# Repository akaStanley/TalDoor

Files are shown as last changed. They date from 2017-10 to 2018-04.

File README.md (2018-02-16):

# TalDoor (GatekeeperV2)
Spencer Kulbacki ~ CSH 2017-18

TalDoor (or GatekeeperV2) is a small POE door lock system that runs off the PocketBeagle and uses PN532 NFC module to scan and authenticate user ID cards and open the door.

## Hardware:
- [PocketBeagle](https://github.com/beagleboard/pocketbeagle)
- Pn532 NFC Module
- Esimated 500mA consumption of entire device during idle operation. Peak of 800mA during read/write  door motor operations. EST less than 3 WATT max POE requirements.

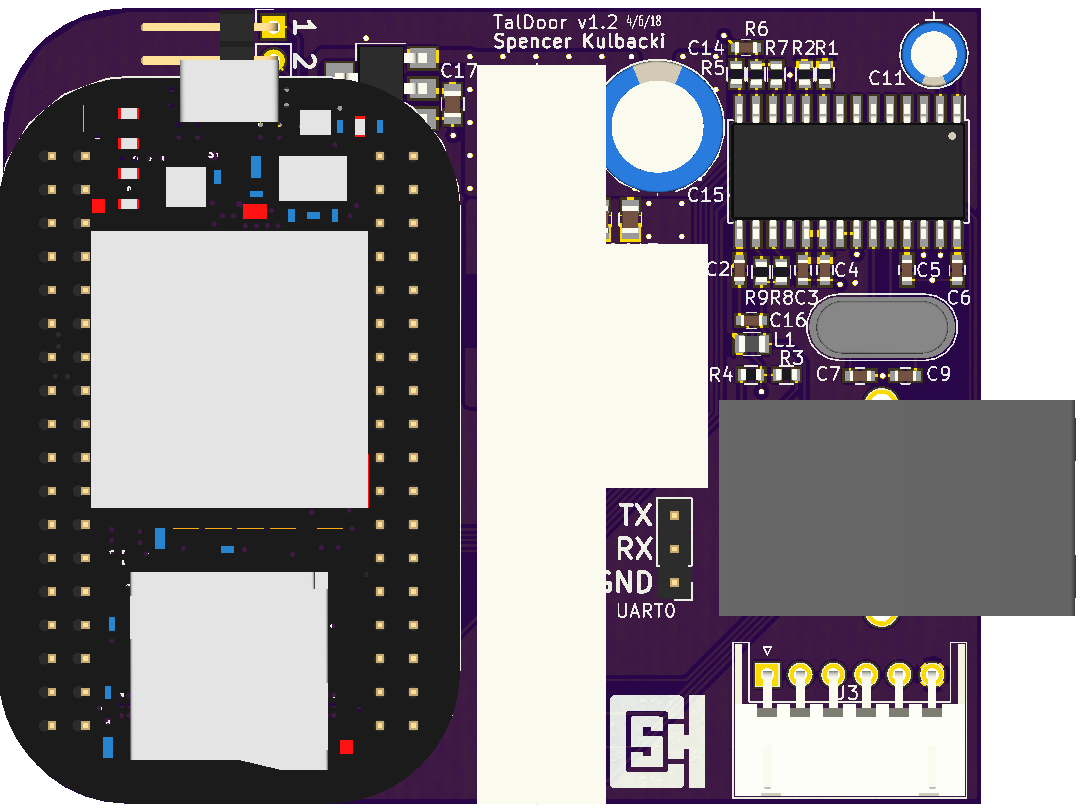
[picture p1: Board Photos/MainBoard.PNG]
Version 1.1 of the Main Board PCB.
  
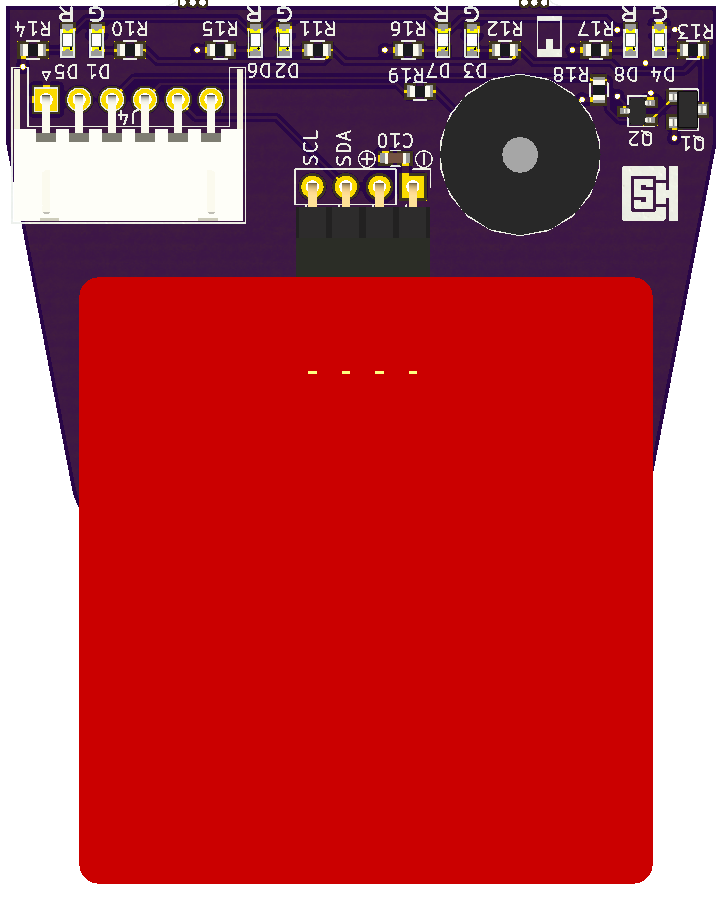
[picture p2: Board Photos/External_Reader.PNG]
Version 1.1 of the NFC Reader PCB.
  
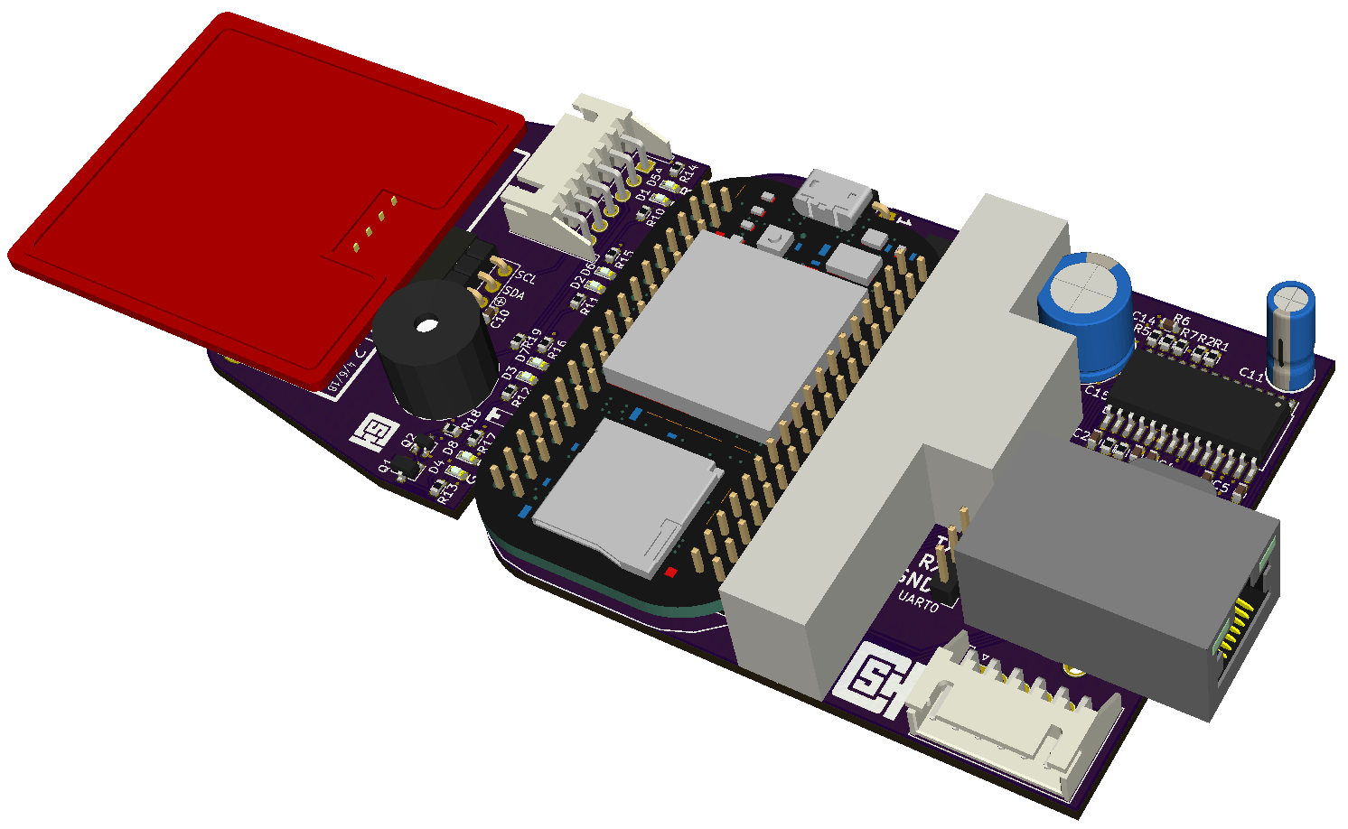
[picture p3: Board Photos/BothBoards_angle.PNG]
Version 1.1.
  

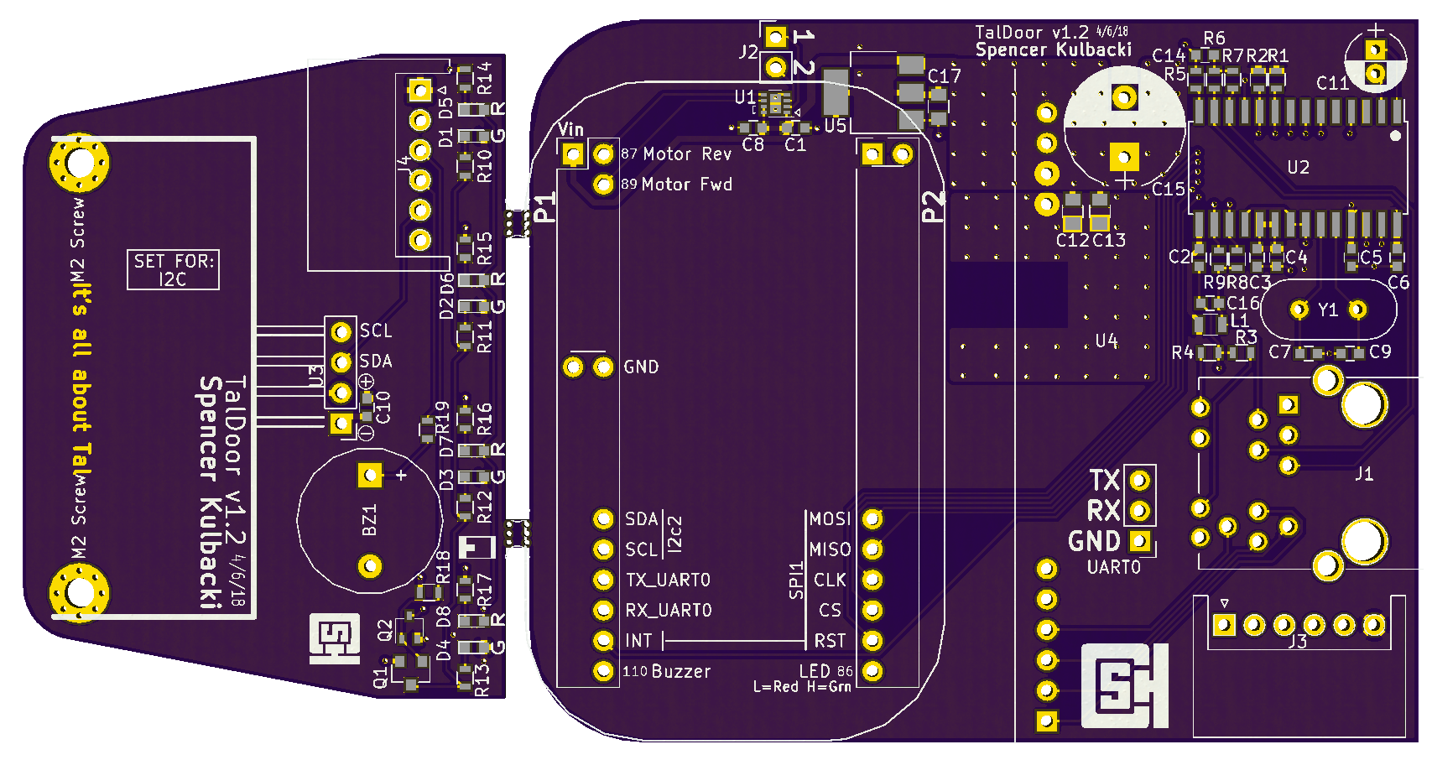
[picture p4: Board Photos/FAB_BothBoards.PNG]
Version 1.1 of the PCB.
  

### Internal Main Board contains:
- PocketBeagle
- POE module
- Ethernet to SPI module
- Door lock motor driver
- 3.3 to 5v step up for motor drive
	
### External Reader Board contains:
- PN532 NFC reader
- Red/Green LEDs & Beeper for notification

### Part List for the PCB
+/- some pin headers we already have
~30$ in components for one board (+PCB Cost)

~62 components specified in BOM (not counting extra male pin headers)

QTY|Value
----|------
1|Buzzer
9|0.1uF
2|18pF
3|10uF
1|10000pF
1|10uF
1|470uF
3|1uF
4|G_LED
4|R_LED
1|SI-52003-F_RJ45
1|Conn_01x02
2|Conn_01x06_Male
1|Ferrite_Bead
1|PocketBeagle
1|RK7002BM
1|BSS223PWH6327XTSA1
1|100kΩ
2|10kΩ
2|180Ω
1|2.2kΩ
4|49.9Ω
8|68Ω
1|150Ω
1|DRV8837
1|ENC28J60-I/SO
1|PN532
1|AG9703
1|NCP1117-3.3
1|25MHz

## Software:
- LibNFC 1.7.1

## Notes
- [Paul's Github notes](https://github.com/woo2/gatekeeper-v2/tree/master/notes)
- [BestCo door lock info,sorta](http://www.bestaccess.com/files/6014/6184/1926/WMseries_WEB.pdf)
- Setting up ethernet forwarding over USB for BeagleBone dev on a PC
	- Plugin the BeagleBone to a USB port on your computer
	- Install the drivers
	- In control panel -> Adapter settings, set the IP address of the USB adapter to 192.168.7.1
	- On the adapter that has the internet connection, enable connection sharing with the USB adapter connection
	- ssh into the BeagleBone (ssh 192.168.7.2)
	- Run command "route add default gw 192.168.7.1"
	- Edit /etc/resolv.conf and add the Google name server by adding the line "nameserver 8.8.8.8"
	
- Door locks are 5v motors that need ~70mA to turn a worm gear and "unlock" the turnkey.
- BeagleBoard uses 130mA nom (300mA peak)
- 4 Red 0603 LEDs use 80mA
- ENC28J60-I/SO uses 120mA nom (180mA peak)
- PN532 91mA nom (140mA peak)
- Esimated 500mA consumption of entire device during idle operation. Peak of 800mA during read/write  door motor operations. EST less than 3 WATT max POE requirements.

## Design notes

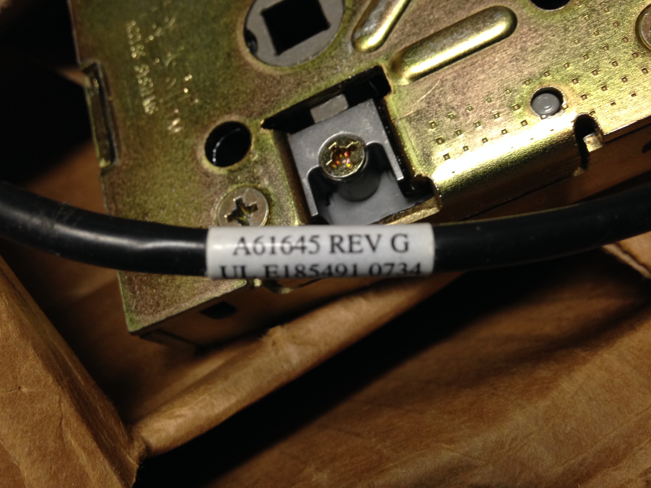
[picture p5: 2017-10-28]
Hardware/Reference/door_lock_motor_info (2).JPG

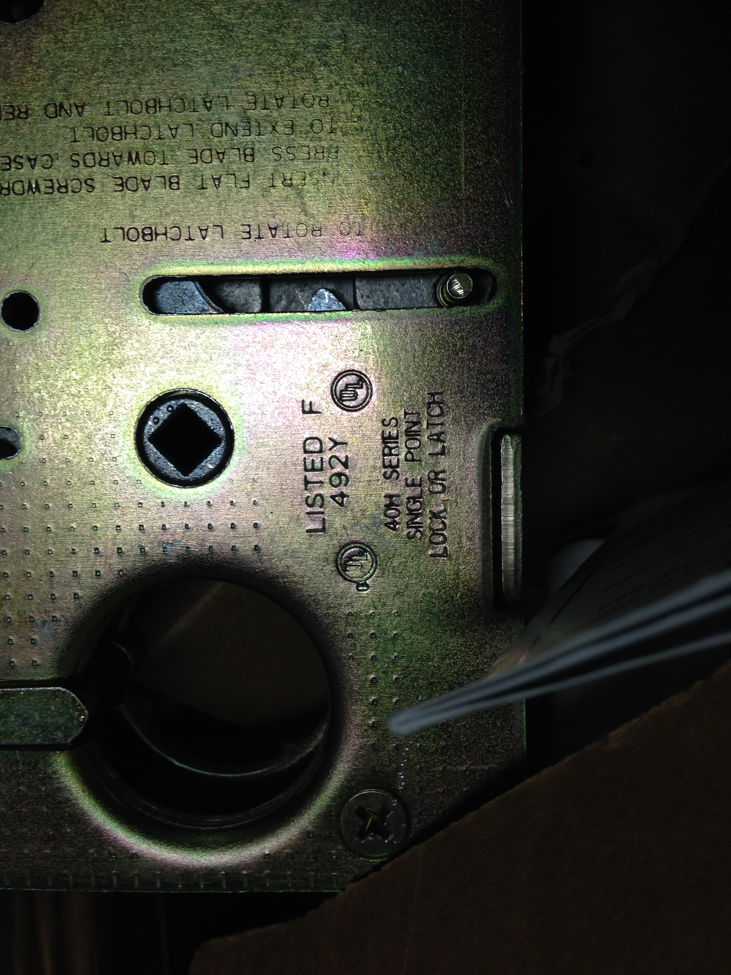
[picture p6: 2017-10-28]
Hardware/Reference/door_lock_motor_info (1).JPG

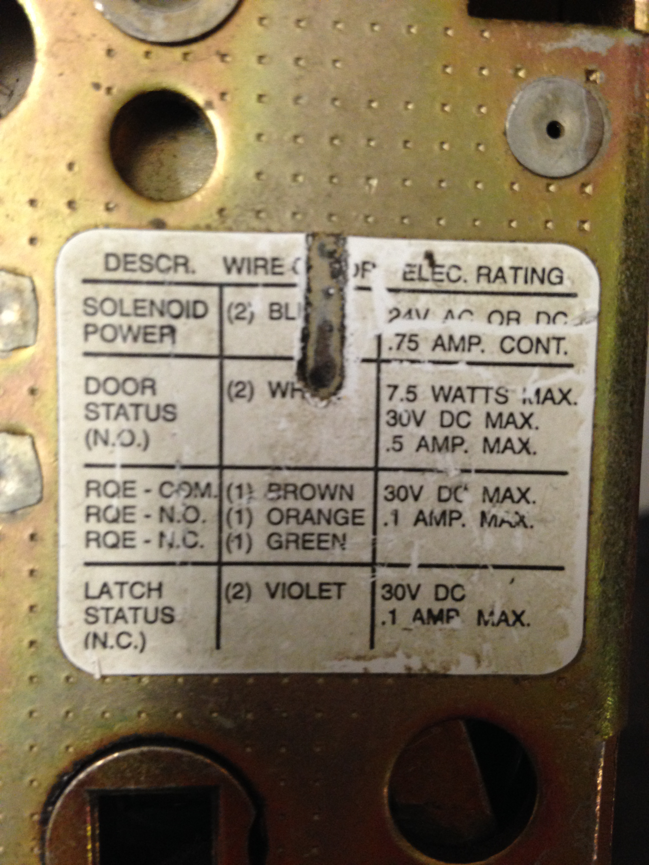
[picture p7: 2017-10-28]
Hardware/Reference/door_lock_motor_info.JPG

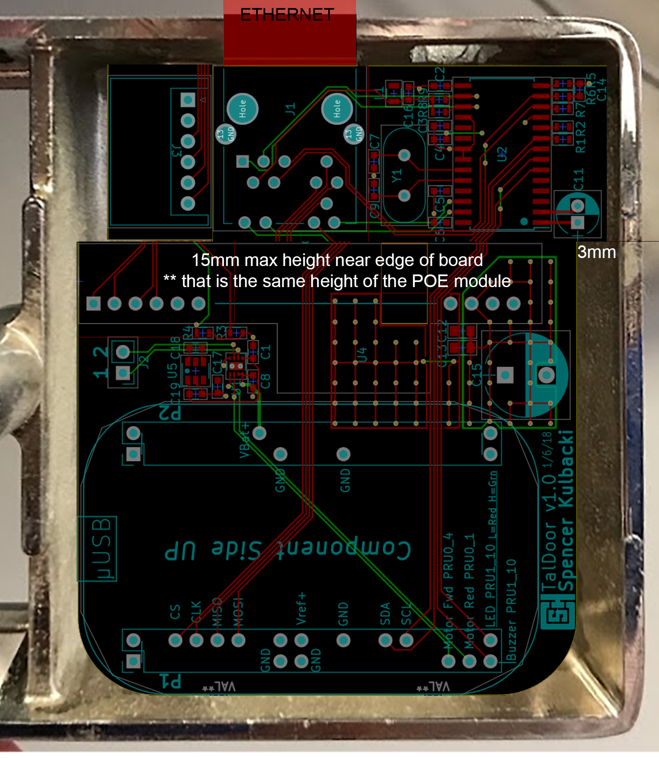
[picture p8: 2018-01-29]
Hardware/Reference/Taldoor_Layout.png

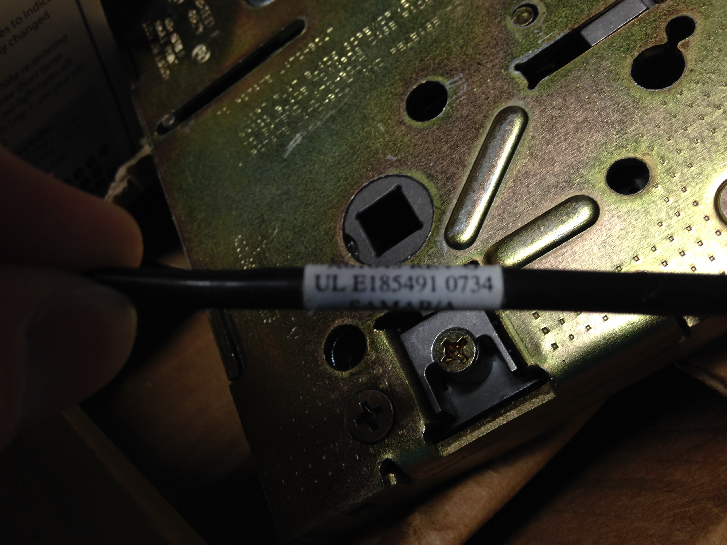
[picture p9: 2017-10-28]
Hardware/Reference/door_lock_motor_info (3).JPG

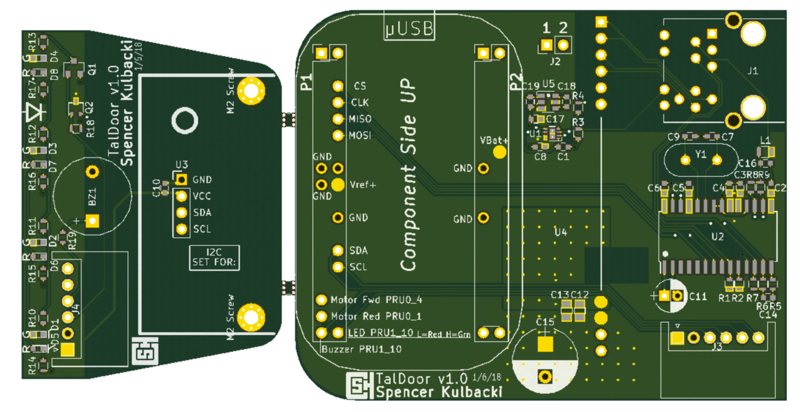
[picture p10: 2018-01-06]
Board Photos/FAB_BothBoards_v1.PNG

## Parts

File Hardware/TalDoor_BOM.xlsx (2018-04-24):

TalDoor PCB
Generated: 4/8/2018 11:51:53 AM | 59
Component Count: | 59
Ref | QTY | Value | Footprint | Description | Digikey Part # | Per Unit | Cost | Notes
BZ1, | 1 | Buzzer | Buzzers_Beepers:Buzzer_12x9.5RM7.6 | Buzzer, polar | 668-1456-ND | 1.375 | 1.3750
C2, C3, C4, C5, C6, C16, C1, C8, C10, | 9 | 0.1uF | Capacitors_SMD:C_0603 | Unpolarized capacitor | 478-10054-1-ND | 0.0106 | 0.0954
C7, C9, | 2 | 18pF | Capacitors_SMD:C_0603 | Unpolarized capacitor | 1276-1089-1-ND | 0.0119 | 0.0238
C12, C13, C17 | 3 | 10uF | Capacitors_SMD:C_0805 | Unpolarized capacitor | 1276-1096-1-ND | 0.094 | 0.2820
C14, | 1 | 10000pF | Capacitors_SMD:C_0603 | Unpolarized capacitor | 1276-1132-1-ND | 0.0075 | 0.0075
C11, | 1 | 10uF | Capacitors_THT:CP_Radial_D5.0mm_P2.00mm | Polarised capacitor | 399-6597-ND | 0.105 | 0.1050
C15, | 1 | 470uF | Capacitors_THT:CP_Radial_D10.0mm_P5.00mm | Polarised capacitor | 493-11709-1-ND | 0.311 | 0.3110 | OLD taller one: 493-5907-1-ND
D2, D1, D3, D4, | 4 | G_LED | LEDs:LED_0603 | Green LED | VLMG1300-GS08CT-ND | 0.337 | 1.3480
D5, D6, D7, D8, | 4 | R_LED | LEDs:LED_0603 | Super Red LED | VLMS1300-GS08CT-ND | 0.317 | 1.2680
J1, | 1 | SI-52003-F_RJ45 | TalDoor_Footprints:RJ45_POE | TH RJ45 with transformer + leds | 380-1119-ND | 5.11 | 5.1100 | No EMI Fingers, but different pinout: ARJ11D-MDSD-A-B-FLT2-ND
J2, | 1 | Conn_01x02 | Pin_Headers:Pin_Header_Straight_1x02_Pitch2.54mm | Generic connector, single row, 01x02 |  |  | 0.0000
J4, J3, | 2 | Conn_01x06_Male | Connectors_JST:JST_XH_S06B-XH-A_06x2.50mm_Angled | Generic connector, single row, 01x06 | 455-2236-ND | 0.368 | 0.7360 | Cables: https://www.amazon.com/uxcell-2-54mm-JST-XH-Adapter-Extension/dp/B014IZWGGI
L1, | 1 | Ferrite_Bead | Inductors_SMD:L_0805 | Ferrite bead | 490-7821-1-ND | 0.141 | 0.1410
P1 | 1 | PocketBeagle | TalDoor_Footprints:PocketBeagle_TalDoor | double row, odd1/even2 numbering |  |  | 0.0000 | Bespoke Female/Male Pin Headers (SIP sockets?)
Q1, | 1 | RK7002BM | TO_SOT_Packages_SMD:SOT-23 | Transistor N-MOSFET (general) | RK7002BMT116CT-ND | 0.16 | 0.1600 | Nmos
Q2, | 1 | BSS223PWH6327XTSA1 | TO_SOT_Packages_SMD:SOT-323_SC-70 | P-MOSFET with substrate diode BSS223PWH6327XTSA1 | BSS223PWH6327XTSA1CT-ND | 0.303 | 0.3030 | Pmos
R1, | 1 | 100kΩ | Resistors_SMD:R_0603 | Resistor | CR0603-JW-104ELFCT-ND | 0.008 | 0.0080
R2, R18, | 2 | 10kΩ | Resistors_SMD:R_0603 | Resistor | CR0603-JW-103ELFCT-ND | 0.016 | 0.0320
R3, R4, | 2 | 180Ω | Resistors_SMD:R_0603 | Resistor | RMCF0603JT180RCT-ND | 0.013 | 0.0260
R5, | 1 | 2.2kΩ | Resistors_SMD:R_0603 | Resistor | CR0603-JW-222ELFCT-ND | 0.016 | 0.0160
R9, R8, R7, R6, | 4 | 49.9Ω | Resistors_SMD:R_0603 | Resistor | CR0603-FX-49R9ELFCT-ND | 0.0099 | 0.0396
R14, R10, R11, R12, R15, R16, R13, R17, | 8 | 68Ω | Resistors_SMD:R_0603 | Resistor | CR0603-JW-680ELFCT-ND | 0.016 | 0.1280
R19, | 1 | 120Ω | Resistors_SMD:R_0603 | Resistor | CR0603-JW-121ELFCT-ND | 0.016 | 0.0160
U1, | 1 | DRV8837 | Housings_SON:WSON-8_1EP_2x2mm_Pitch0.5mm_ThermalVias | IC MOTOR DRIVER, 2 Half bridges | 296-34806-1-ND | 1.231 | 1.2310
U2, | 1 | ENC28J60-I/SO | Housings_SOIC:SOIC-28W_7.5x17.9mm_Pitch1.27mm | ENC28J60 Single Chip Ethernet Interface, SOIC-28 | ENC28J60-I/SO-ND | 2.756 | 2.7560
U3, | 1 | PN532 | Pin_Headers:Pin_Header_Straight_1x04_Pitch2.54mm | Pn532 NFC reader over I2C |  | 6.63 | 6.6300 | PN532
U4, | 1 | AG9705 | TalDoor_Footprints:Ag9700_FP | 48v POE stepdown transformer and voltage supply |  | 7.29 | 7.2900 | Ag9705-2BR
U5, | 1 | NCP1117-3.3_SOT223 | TO_SOT_Packages_SMD:SOT-223-3_TabPin2 | 1A Low Dropout regulator, positive, 1.5V fixed output, SOT-223 | 497-1228-1-ND | 0.603 | 0.6030
Y1, | 1 | 25MHz | Crystals:Crystal_HC49-4H_Vertical | Two pin crystal | 631-1112-ND | 0.32 | 0.3200
 |  |  |  |  |  | 30.3613

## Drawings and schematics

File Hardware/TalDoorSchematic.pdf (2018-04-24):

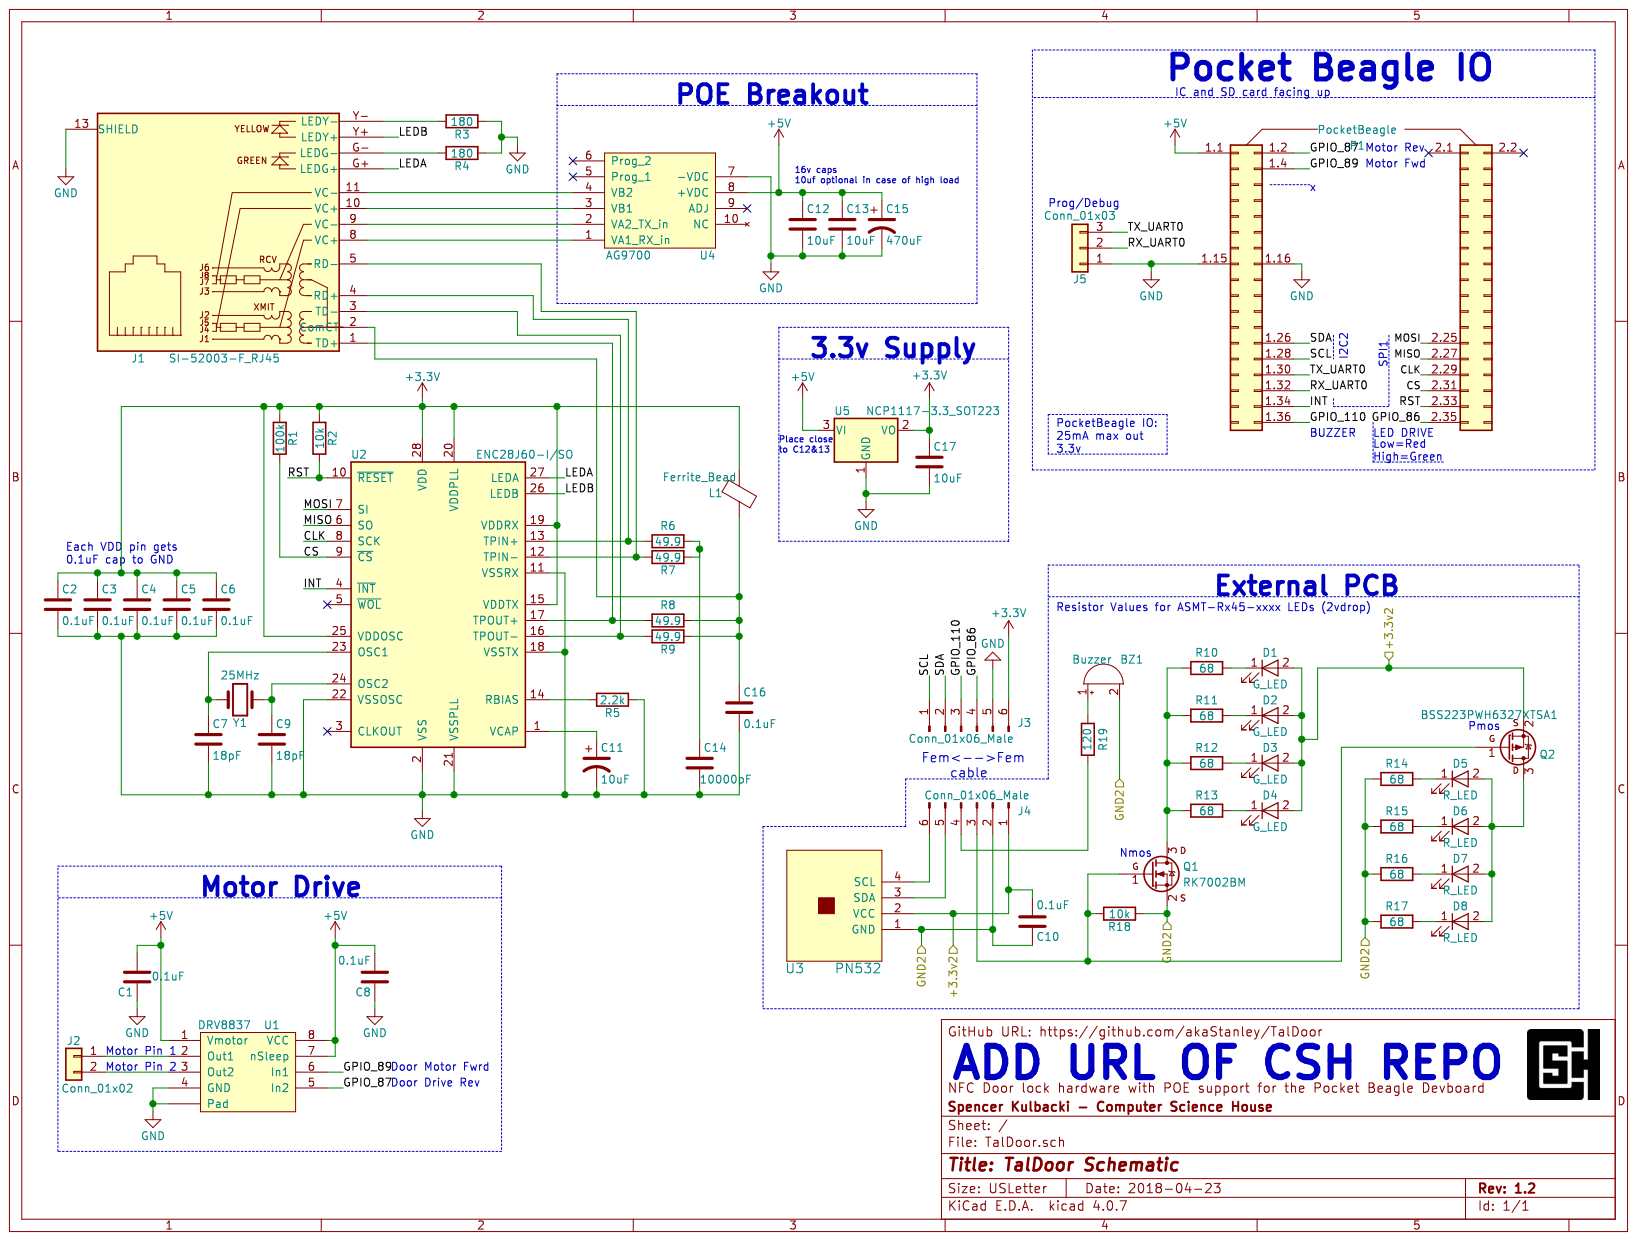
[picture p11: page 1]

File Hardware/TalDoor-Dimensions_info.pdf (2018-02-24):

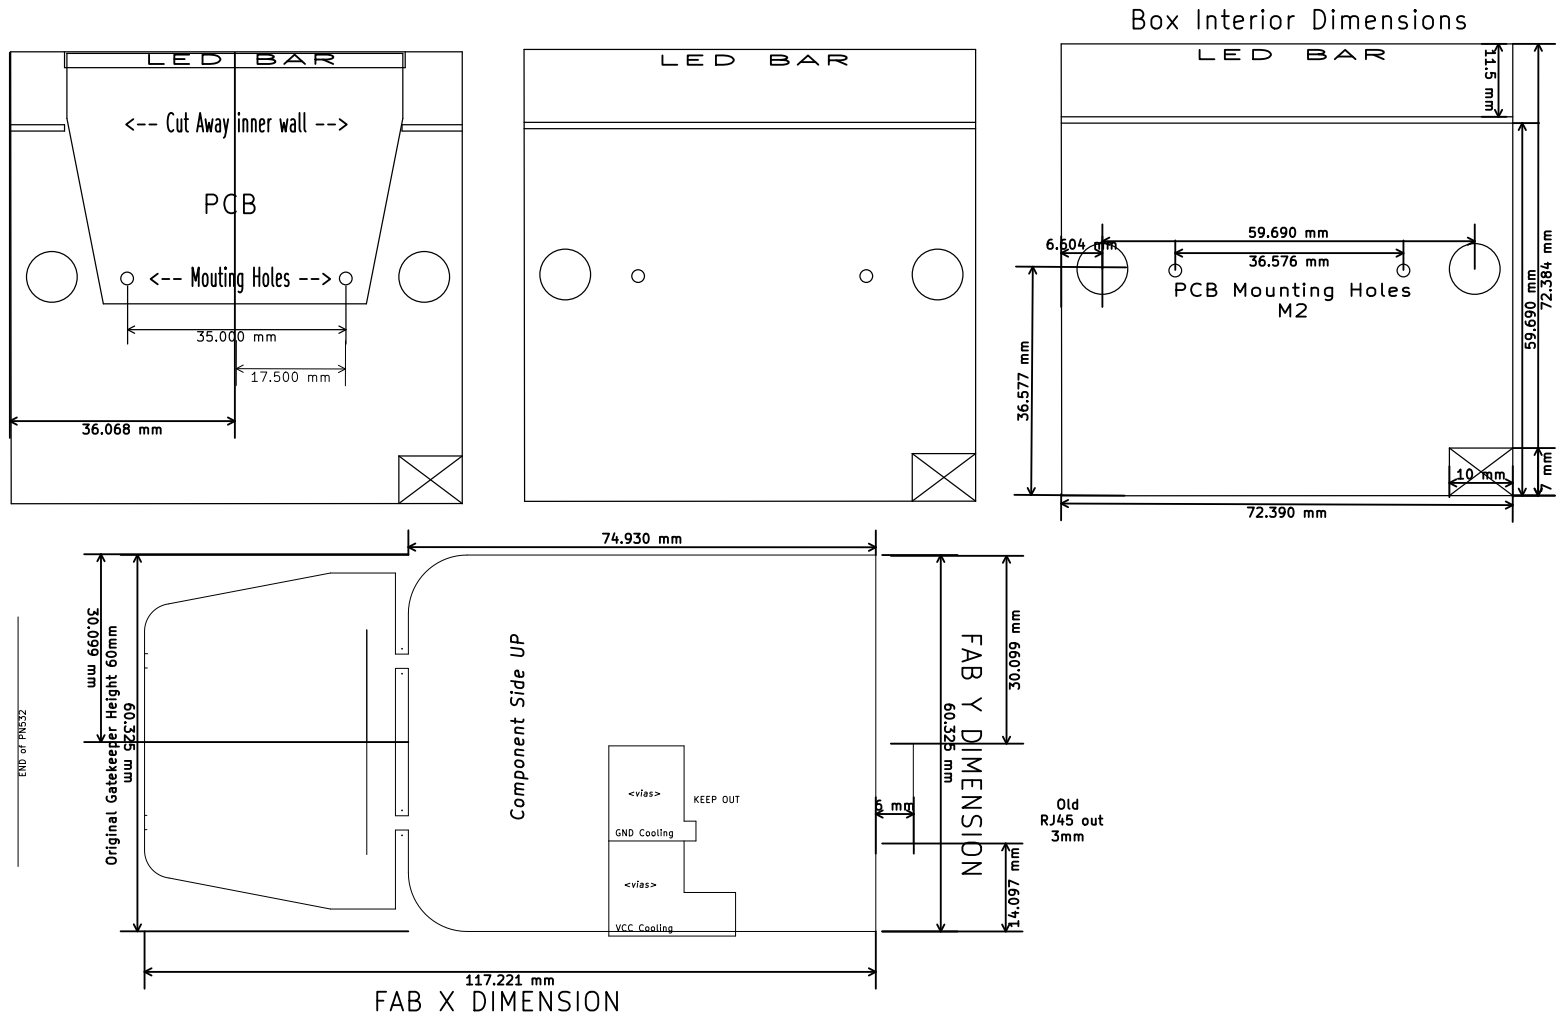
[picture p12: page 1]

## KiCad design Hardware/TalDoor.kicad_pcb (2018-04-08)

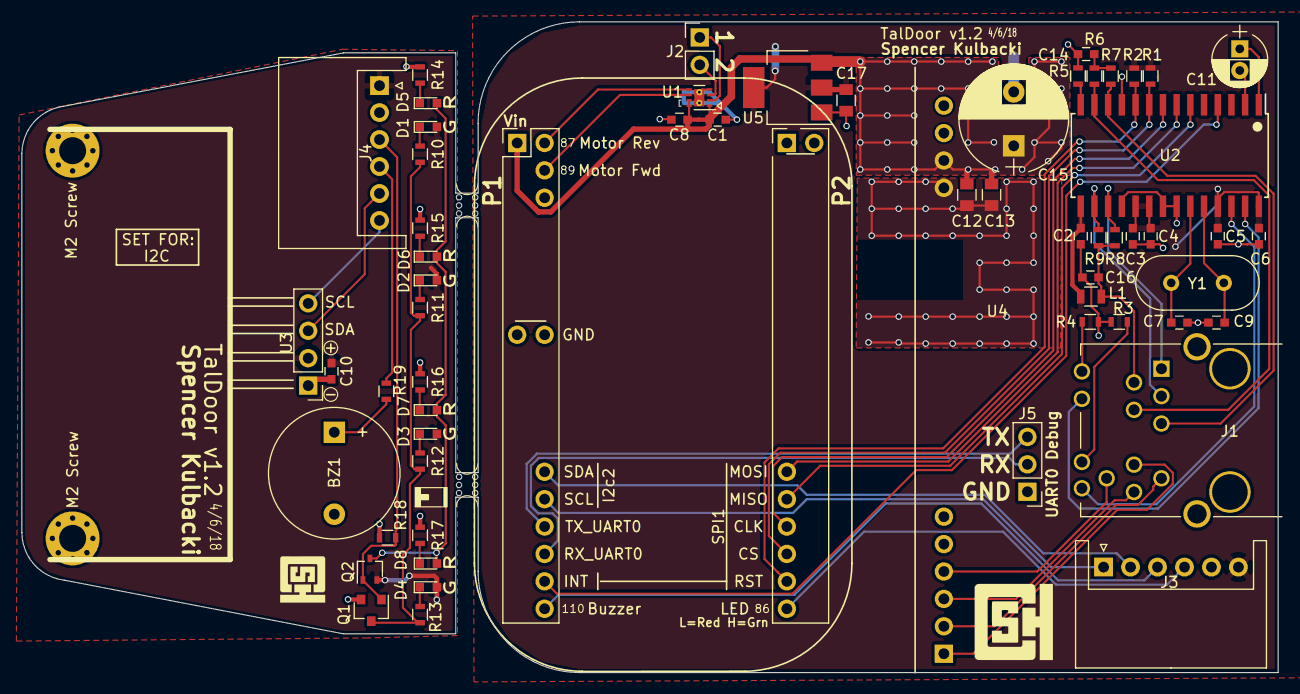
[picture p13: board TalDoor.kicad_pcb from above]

Board: 2 copper layers, 116.5 x 60.3 mm, 64 parts (0 on the bottom side), 54 nets.

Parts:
BZ1: Buzzer; Buzzer_12x9.5RM7.6
C1, C2, C3, C4, C5, C6, C8, C10, C16: 0.1uF; C_0603
C7, C9: 18pF; C_0603
C11: 10uF; CP_Radial_D5.0mm_P2.00mm
C12, C13, C17: 10uF; C_0805
C14: 10000pF; C_0603
C15: 470uF; CP_Radial_D10.0mm_P5.00mm
D1, D2, D3, D4: G_LED; LED_0603
D5, D6, D7, D8: R_LED; LED_0603
J1: SI-52003-F_RJ45; RJ45_POE
J2: Conn_01x02; Pin_Header_Straight_1x02_Pitch2.54mm
J3, J4: Conn_01x06_Male; JST_XH_S06B-XH-A_06x2.50mm_Angled
J5: Conn_01x03; Pin_Header_Straight_1x03_Pitch2.54mm
L1: Ferrite_Bead; L_0805
M2 Screw, M2 Screw#2: MountingHole_2.2mm_M2_Pad_Via; MountingHole_2.5mm_Pad_Via
P1: PocketBeagle; PocketBeagle_TalDoor
Q1: RK7002BM; SOT-23
Q2: BSS223PWH6327XTSA1; SOT-323_SC-70
R1: 100k; R_0603
R2, R18: 10k; R_0603
R3, R4: 180; R_0603
R5: 2.2k; R_0603
R6, R7, R8, R9: 49.9; R_0603
R10, R11, R12, R13, R14, R15, R16, R17: 68; R_0603
R19: 120; R_0603
U1: DRV8837; WSON-8_1EP_2x2mm_Pitch0.5mm_ThermalVias
U2: ENC28J60-I/SO; SOIC-28W_7.5x17.9mm_Pitch1.27mm
U3: PN532
U4: AG9700; Ag9700_FP
U5: NCP1117-3.3_SOT223; SOT-223-3_TabPin2
Y1: 25MHz; Crystal_HC49-4H_Vertical
mouse-bite-2mm-slot, mouse-bite-2mm-slot#2: VAL**; mouse-bite-2mm-slot

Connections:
+3V3: C2.1, C3.1, C4.1, C5.1, C6.1, C17.1, J3.6, L1.2, R1.1, R2.1, U2.15, U2.19, U2.20, U2.25, U2.28, U5.2
+5V: C1.2, C8.2, C12.1, C13.1, C15.1, P1.1.1, U1.1, U1.7, U1.8, U4.8, U5.3
/+3.3v2: C10.2, D1.2, D2.2, D3.2, D4.2, J4.1, Q2.2, U3.2
/CLK: P1.2.29, U2.8
/CS: P1.2.31, R1.2, U2.9
/GND2: BZ1.2, C10.1, J4.2, Q1.2, R14.2, R15.2, R16.2, R17.2, R18.1, U3.1
/GPIO_86: J3.4, P1.2.35
/GPIO_87: P1.1.2, U1.5
/GPIO_89: P1.1.4, U1.6
/GPIO_110: J3.3, P1.1.36
/INT: P1.1.34, U2.4
/LEDA: J1.G+, U2.27
/LEDB: J1.Y+, U2.26
/MISO: P1.2.27, U2.6
/MOSI: P1.2.25, U2.7
/RST: P1.2.33, R2.2, U2.10
/RX_UART0: J5.2, P1.1.32
/SCL: J3.1, P1.1.28
/SDA: J3.2, P1.1.26
/TX_UART0: J5.3, P1.1.30
GND: C1.1, C2.2, C3.2, C4.2, C5.2, C6.2, C7.2, C8.1, C9.2, C11.2, C12.2, C13.2, C14.2, C15.2, C16.2, C17.2, J1.13, J3.5, J5.1, P1.1.15, P1.1.16, R3.1, R4.1, R5.1, U1.4, U2.2, U2.11, U2.18, U2.21, U2.22, U4.7, U5.1
unnamed: BZ1.1, R19.2
unnamed: C7.1, U2.23, Y1.2
unnamed: C9.1, U2.24, Y1.1
unnamed: C11.1, U2.1
unnamed: C14.1, R6.1, R7.1
unnamed: C16.1, J1.2, L1.1, R8.1, R9.1
unnamed: D1.1, R10.1
unnamed: D2.1, R11.1
unnamed: D3.1, R12.1
unnamed: D4.1, R13.1
unnamed: D5.1, R14.1
unnamed: D5.2, D6.2, D7.2, D8.2, Q2.3
unnamed: D6.1, R15.1
unnamed: D7.1, R16.1
unnamed: D8.1, R17.1
unnamed: J1.1, R8.2, U2.17
unnamed: J1.3, R9.2, U2.16
unnamed: J1.4, R6.2, U2.13
unnamed: J1.5, R7.2, U2.12
unnamed: J1.8, U4.1
unnamed: J1.9, U4.2
unnamed: J1.10, U4.3
unnamed: J1.11, U4.4
unnamed: J1.G-, R4.2
unnamed: J1.Y-, R3.2
unnamed: J2.1, U1.2
unnamed: J2.2, U1.3
unnamed: J4.3, Q1.1, Q2.1, R18.2
unnamed: J4.4, R19.1
unnamed: J4.5, U3.3
unnamed: J4.6, U3.4
unnamed: Q1.3, R10.2, R11.2, R12.2, R13.2
unnamed: R5.2, U2.14

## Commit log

2017-10-31 added LED links
2017-12-28 Started KiCad Schematic. Added project specific parts library. linked some datasheets
    [PCB.kicad_pcb, PCB.sch]
2017-12-29 Added parts for Ethernet jack and PocketBeagle IO
    [PCB.sch]
2017-12-29 Added all parts but motor drive. updated readme parts list
    [PCB.sch]
2017-12-29 added motor driver
    [PCB.sch]
2017-12-29 cleaned up some of schematic
    [PCB.sch]
2017-12-31 Added footprints to all parts
    [TalDoor.kicad_pcb, TalDoor.sch]
2018-01-02 generated BOM with pricing
    [TalDoor_BOM.xlsx]
2018-01-02 started PCB, added 3d models for all parts
    [TalDoor_BOM.xlsx]
2018-01-03 Added connectors, moved notifications to external PCB
    [TalDoor.kicad_pcb, TalDoor.sch, TalDoor_BOM.xlsx]
2018-01-04 Solution to 1 wire LED nitification issue. See LED_NotificationModel.txt
    [TalDoor.kicad_pcb, TalDoor.sch, TalDoor_BOM.xlsx]
2018-01-04 Updated schematic with N/Pmos LED format for single IO drive. Updated BOM
    [TalDoor.kicad_pcb, TalDoor.sch, TalDoor_BOM.xlsx]
2018-01-05 Secondary PCB layout complete
    [TalDoor.kicad_pcb, TalDoor.sch]
2018-01-05 adding measurements for main PCB
    [TalDoor.kicad_pcb, TalDoor.sch]
2018-01-06 Completed Mainboard PCB, needs Vgroove/Mousebite connection between two. Also check motor driver
    [TalDoor.sch, TalDoor_BOM.xlsx]
2018-01-06 Added PCB Photos and Schematic PDFs for info
    [TalDoor.kicad_pcb, TalDoor.sch]
2018-01-06 Added 5v motor control. Updated schematic, images, BOM, PCB layout
    [TalDoor.kicad_pcb, TalDoor.sch, TalDoor_BOM.xlsx]
2018-01-06 updated PCB
    [TalDoor.kicad_pcb]
2018-01-08 updated bom
    [TalDoor_BOM.xlsx]
2018-01-29 Started changed base on Hardware 1 build
    [TalDoor.kicad_pcb, TalDoor.sch, TalDoor_BOM.xlsx]
2018-01-29 generated new bom file, need to be combined and updated with old one.
    [TalDoor_new_temp_bom.csv]
2018-02-03 Updating PCB layout, unfinished
    [TalDoor.kicad_pcb, TalDoor.sch, TalDoor_BOM.xlsx]
2018-02-03 fixed fills so there is no DRC error
    [TalDoor.kicad_pcb]
2018-02-12 Updated PCB layout for fixes from v1
    [TalDoor.kicad_pcb, TalDoor.sch]
2018-02-16 Updated PCB with solder jumpers for easier developing
    [TalDoor.kicad_pcb, TalDoor.sch]
2018-02-16 Updated board photos and readme
2018-02-17 ordered V1.1 boards
    [TalDoor.kicad_pcb, TalDoor_BOM.xlsx]
2018-02-17 updated part number
    [TalDoor_BOM.xlsx]
2018-02-24 Updated Drawings and schematic pdfs
2018-03-09 updated schematic rev & date, bom
    [TalDoor.sch, TalDoor_BOM.xlsx]
2018-03-10 updated layout to account for door mount shape issue
    [TalDoor.kicad_pcb, TalDoor_BOM.xlsx]
2018-04-07 fixed ethernet module, SPI, I2c busses
    [TalDoor.kicad_pcb, TalDoor.sch, TalDoor_BOM.xlsx]
2018-04-08 Updated PCB and added new photos
    [TalDoor.kicad_pcb]
2018-04-24 updated schematic
    [TalDoor.sch, TalDoor_BOM.xlsx]
